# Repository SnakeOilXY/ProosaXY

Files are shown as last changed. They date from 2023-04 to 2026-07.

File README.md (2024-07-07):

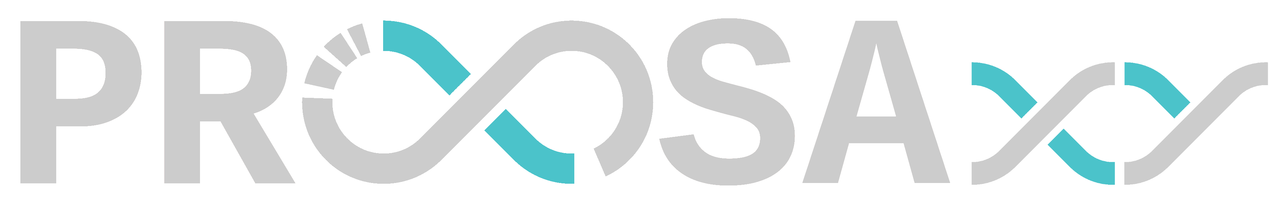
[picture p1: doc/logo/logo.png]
baner logo


<a href="https://discord.gg/WZVP2HuAag" style="height: 40px !important;">Join us on Discord</a>

<a href='https://www.amazon.jp/hz/wishlist/ls/2AHXTCG01RYAZ?ref_=wl_share' target='_blank'>Buy Me a spool at amazon Japan</a>

# ProosaXY
CoreXY conversion for Prusa MK3/S. This build is aiming at getting more performance out of your 6 years old machine with the lowest cost possible by re-using most the MK3/S stock parts.

## 1. Features

- Better performance (check input-shaper graph bellow).
- Semi-enclosure by default. Panels mount and top hat parts will be added later.
- ~~Dual z axis(default) or independent tripple Z axis(Optional)~~ Triple Z (independent or sync based on controller board) by default or dual Z(optional).
- Single v6 hotend(default) or mixed 2-in-1-out hotend(WIP).
- Optional AUX cooling fan.
- Semi-enclosured(default) or Fully-enclosured with top hat(comming soon).
- Our industrial leading SnakeOil technology :).

## 2. Status

- All the main parts design are completed. Test print result are posted in our [Discord server](https://discord.gg/WZVP2HuAag)
- All part STLs are exported. 
- Full BOM added 2023/07/11
- I'm working on a simple build log/manual. 
- For updates, please visit our [Discord server](https://discord.gg/WZVP2HuAag)

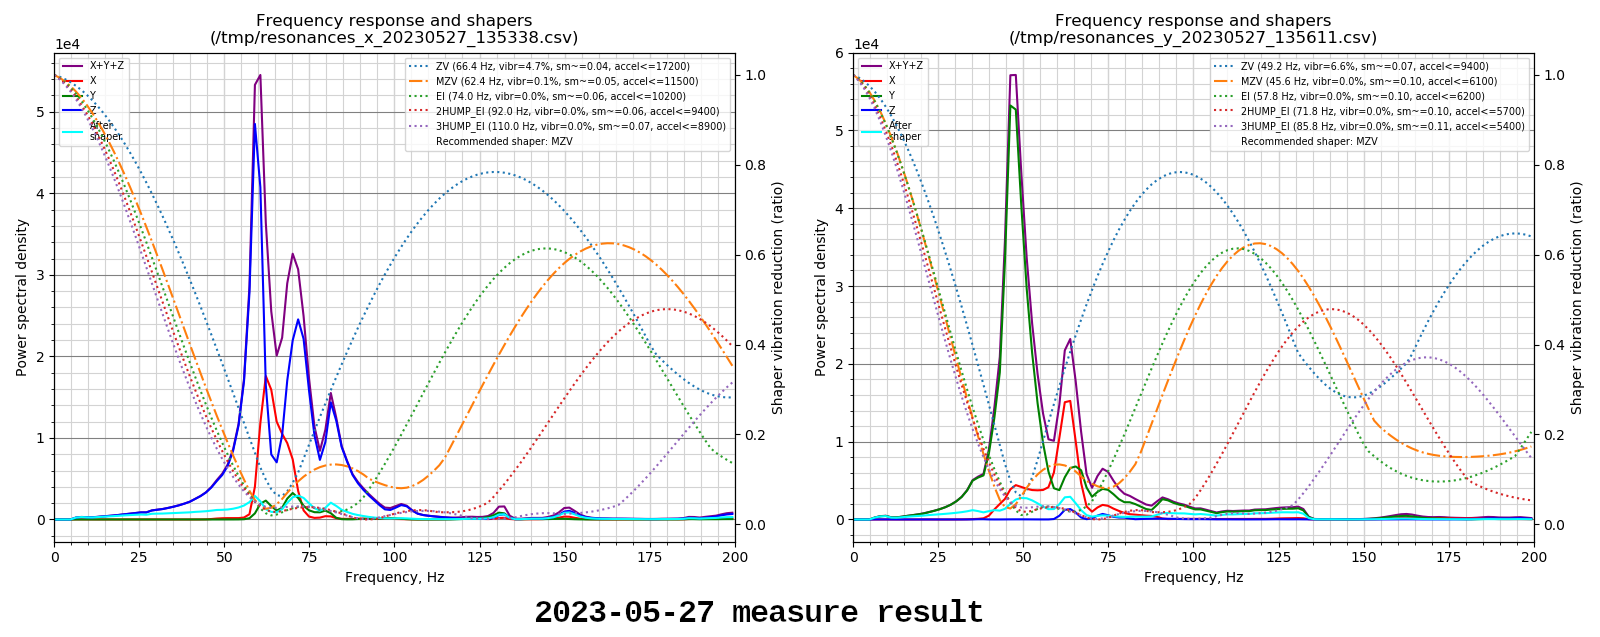
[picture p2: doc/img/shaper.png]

- The input-shaper calibration is quite good for an 8mm shaft machine, in my opinion. We have a recommended acceleration of about 6000 mm/s2 (which should be used as the limit for outer perimeter acceleration), and a higher maximum acceleration/speed, depending on how fast your motor can run.
- For some extra speed boost, check my [slicer plugin](https://github.com/SnakeOilXY/klipper-dynamic-scv-slicer-post-processing) (klipper firmware only)

## 3. Warning - read this

- This mod requires some drilling on the original frame, cutting the original motor leadscrew, and linear shafts. This drilling/cutting is easy enough to be done with a hand drill and a hacksaw **BUT THERE IS NO WAY BACK. You won't be able to convert back to the original MK3/s machine if you change your mind later.**
- Some small changes/patches might be needed after I have more test data and feedback..
- To keep the cost down and reuse old components, there are some trade-offs I made:
    - The machine is semi-enclosed by default and will need some printed panels and a top hats to fully enclose it.
    - To match the frame height, cutting the motor leadscrew and linear shafts is required.

## BOM

[Fabreeko ProosaXY Conversion Kit (Open Beta)](https://www.fabreeko.com/products/proosa-xy-conversion-for-mk3s-to-core-xy-by-snakeoilxy-open-beta) available now.

[>>> Bill of materials <<<](./doc/BOM/readme.md)

## 4. Test run videos and images

### 4.1 Prusa Mk4 12mins bonker benchy 

<table>
    <thead>
        <tr>
            <th></th>
            <th align="center">Mk4 bonker benchy</th>
            <th align="center">Real-world print</th>
        </tr>
    </thead>
    <tbody>
        <tr>
            <td>Video</td>
            <td align="center"><a href="https://youtu.be/1M5wx4Q0jNs" rel="nofollow">
            bonker benchy test print</a></td>
            <td align="center"><a href="https://youtu.be/Dink3JQ" rel="nofollow">
            normal test print</a></td>
        </tr>
        <tr>
            <td>Description</td>
            <td>I use the setting Prusa used on their mk4 12 mins benchy with accel pump up a little.</br>
            <a href="https://github.com/SnakeOilXY/ProosaXY/tree/master/doc/img/bonker-benchy">Print result (images)</a></br>
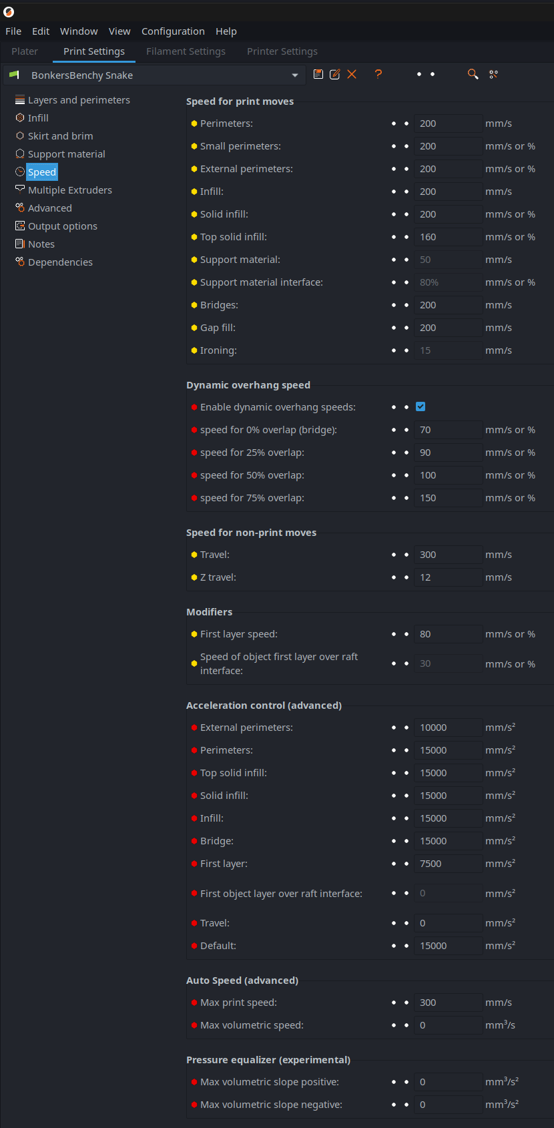
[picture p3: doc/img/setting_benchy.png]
            </td>
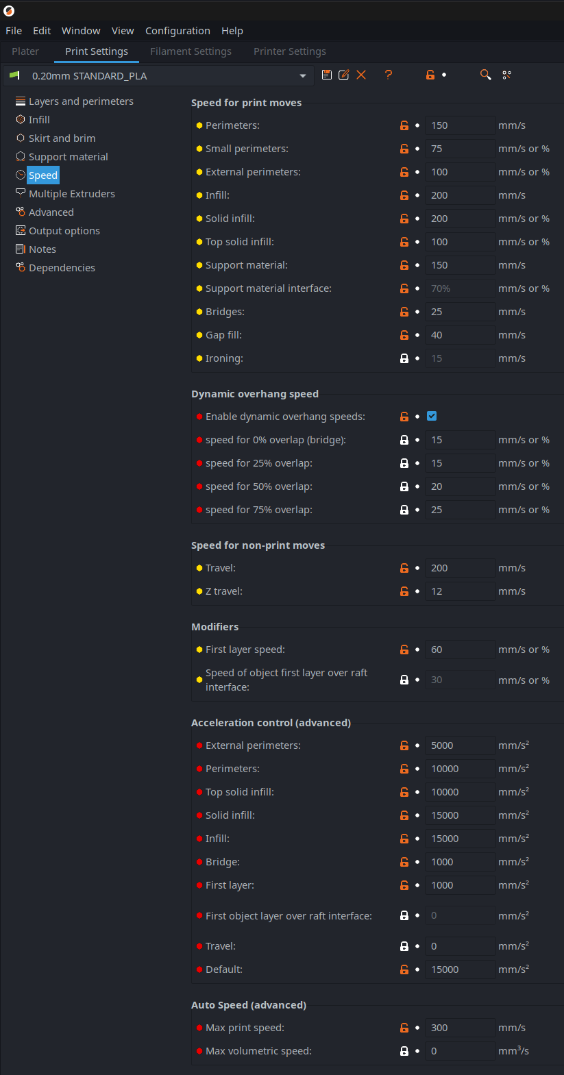
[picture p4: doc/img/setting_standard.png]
            <td></td>
        </tr>
    </tbody>
</table>

### 4.2 Images
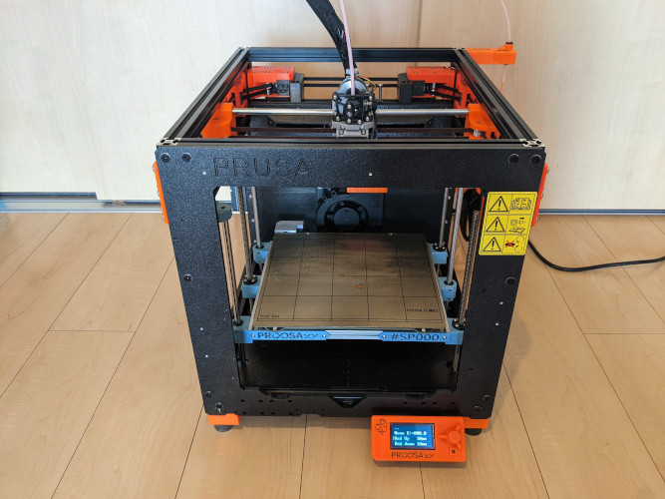
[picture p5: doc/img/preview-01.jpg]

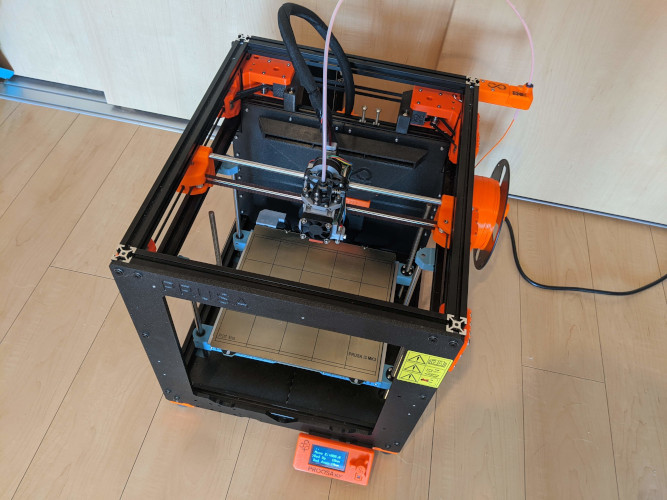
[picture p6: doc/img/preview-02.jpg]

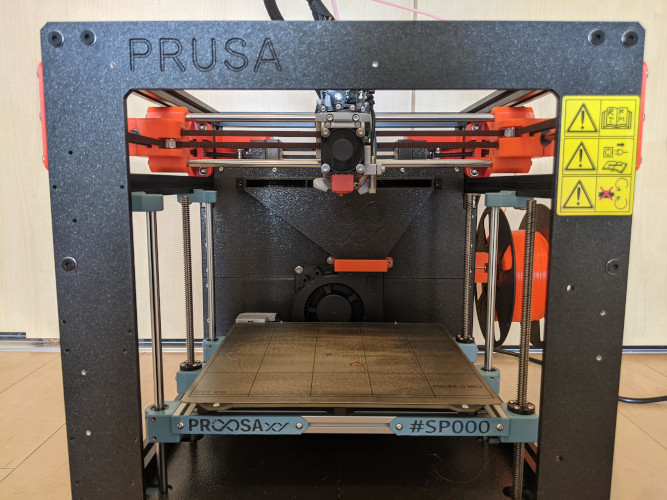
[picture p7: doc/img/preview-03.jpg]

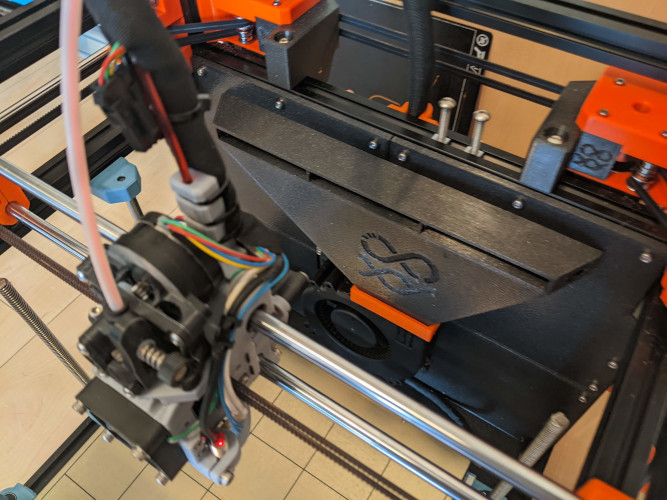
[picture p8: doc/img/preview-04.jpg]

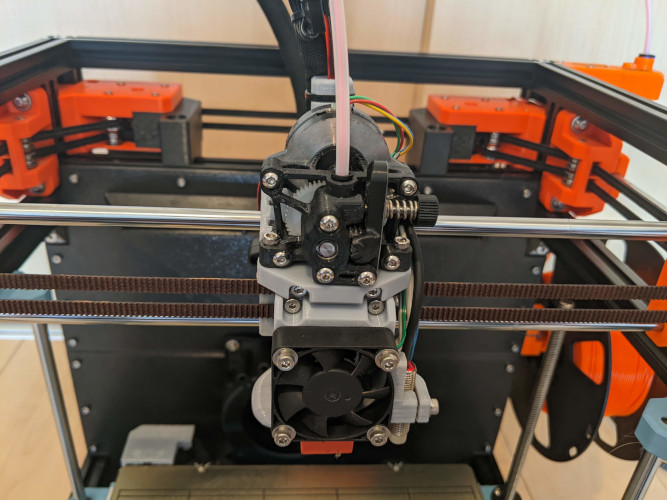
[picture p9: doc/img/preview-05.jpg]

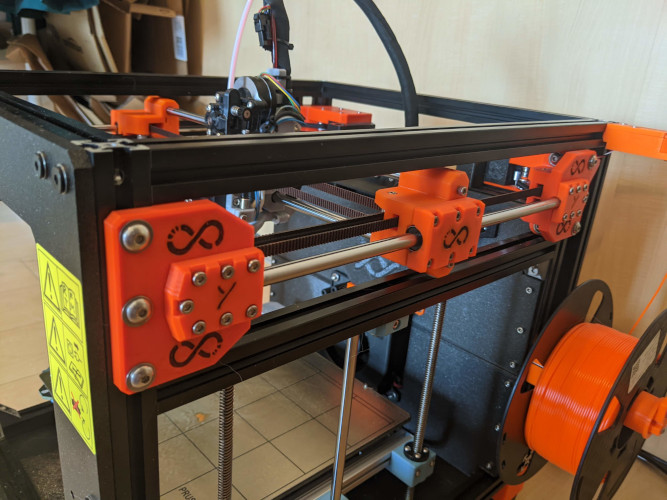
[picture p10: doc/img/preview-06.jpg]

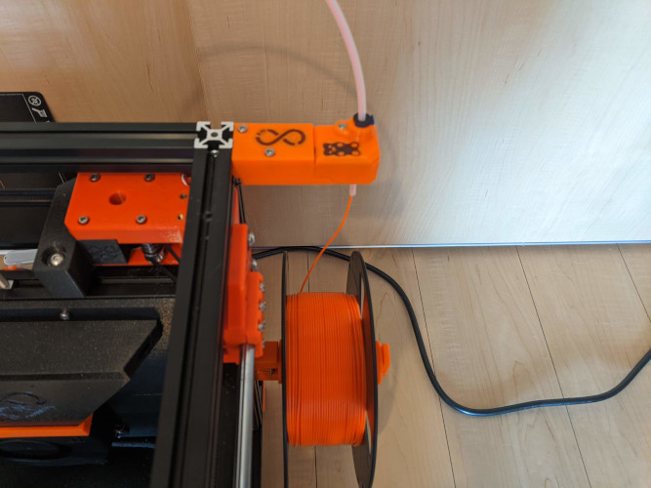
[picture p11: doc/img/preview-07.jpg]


## 5. Copyright Notice

This printer design use the following parts from other opensource project:
- Fan duct from [EVA 2.3](https://github.com/EVA-3D/eva-main)
- Filament sensor from [Bear Extruder And X Axis (BearExxa)](https://github.com/gregsaun/bear_extruder_and_x_axis)
- Sherpa mini extruder from [Annex Engineering](https://github.com/Annex-Engineering/Sherpa_Mini-Extruder)
- Din mounter from [Voron design](https://github.com/VoronDesign)
- Original hardwares from [Prusa MK3](https://github.com/prusa3d/Original-Prusa-i3)

### License

- [Sherpa mini extruder](https://github.com/Annex-Engineering/Sherpa_Mini-Extruder) is an original work of [Annex Engineering](https://github.com/Annex-Engineering), modified parts using their source code/design files are re-released under [ANNEX Engineering License](https://github.com/Annex-Engineering/ANNEX-Engineering-License-Agreement/blob/main/LICENSE.md).
- [EVA2](https://github.com/EVA-3D/eva-main) is an original work of [EVA-3D](https://github.com/EVA-3D), modified parts using their source code/design files are re-released under [GNU General Public License v3.0](https://github.com/EVA-3D/eva-main/blob/main/LICENSE)
- [Bear Extruder And X Axis (BearExxa)](https://github.com/gregsaun/bear_extruder_and_x_axis) is an original work of [Grégoire Saunier](https://github.com/gregsaun), modified parts using their source code/design files are re-released under [GNU General Public License v3.0](https://github.com/gregsaun/bear_extruder_and_x_axis/blob/master/LICENSE)
- [Voron]() is an original work of [Voron design](https://github.com/VoronDesign), modified parts using their source code/design files are re-released under [GNU General Public License v3.0](https://github.com/VoronDesign/Voron-2/blob/Voron2.4/LICENSE)
- [Prusa MK3](https://github.com/prusa3d/Original-Prusa-i3) is an original work of [Prusa3D](https://github.com/prusa3d), modified parts using their source code/design files are re-released under [GNU General Public License v2.0](https://github.com/prusa3d/Original-Prusa-i3/blob/MK3S/LICENSE)
- This printer design(ProosaXY), it's document and software are released under [GNU General Public License v3.0](https://github.com/SnakeOilXY/ProosaXY/blob/master/LICENSE)

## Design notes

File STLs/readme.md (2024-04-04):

# Print setting

## 1.Slicer config

- This is the setting I'm using but any other settings will work as long as the parts are strong enough.
- All STLs are oriented. (Please report if you find problem)
- Make sure your printer well calibrated.

<pre>Layer height : 0.2mm
Wall count : 5
Top/bottom layer : 5
Infill : 30% Gyroid 
Outer wall line width : 0.4mm
Inner wall line width : 0.45mm
Infill line width : 0.5mm
Most of the parts are designed to be printed without support(for exception, check the list bellow). You can enable "support on build plate only" for better overhang surface.
</pre>

### Parts require custom support

| | | |
|---|---|---|
| 3x_pom-nut-mounter.stl | | Need support on build plate |
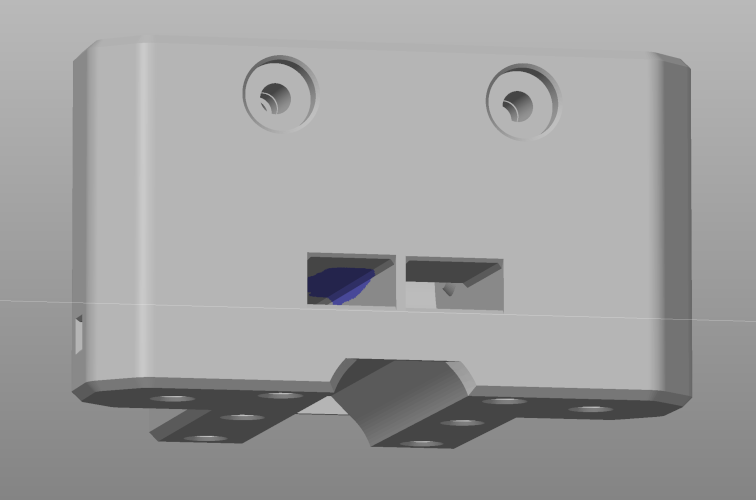
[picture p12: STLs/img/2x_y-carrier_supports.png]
2x_y-carrier_***
| 2x_y-carrier_***.stl |  | Custom support inside the channel due to some thin walls. |
| | | |

## 2.Filament

- PETG and higher temp-resistant filaments will work.
- Motor mount and tool head parts might require higher temp-resistant filament.
- Gillter or CF filled filaments might make the parts more brittle or creep.

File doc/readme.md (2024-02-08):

# Doc

- Extrusions drawing [pdf](./frame/frame-extrusion-drawing.pdf)
- Center frame drawing [pdf](./frame/mk3-center-frame-drilling.pdf)
- Bed frame drawing [pdf](./frame/mk3-bed-frame-drilling.pdf)

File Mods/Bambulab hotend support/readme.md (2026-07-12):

# ProosaXY Bambulab hotend support

The bambulab H2/P2 hotend/nozzles offers a good performance with a competitive price. And we have a bunch of aftermarket for this.

The main idea is to use the A1 heating assembly of aftermarket supplier like mellow or triangle lab.

Both offers Zirconia base plus Cooper block and 96W PTC heater (oem are 48W). Costs around 20-25€

The A1 heating assembly has better wires and known thermistor.

The idea of using H2/P2 nozzles are because they have longer melt distance than the A1 ones.

This idea was impossible to do before due the builtin tensioners, for that reason you need to fit the front belt tensioner mods and a proper X-carrier mod.

This aftermarket heating assembly it's intended to trick bambulab firmware/hardware restrictions that can only deliver 3.5A peak max on heater and later limit to 3A when printing, with this trick they boost the flow rate performance because the limitations made of the standard 48W heater.

We tested with 30mm3/s at 295ºC, the heater was at 50-60% duty cycle.

## IMPORTANT Printing instructions

The 1x_bambulab_fan_pinda_support requires to be printed with 0.15mm layer height, no supports required, they are modeled.

Enable supports for critical regions only on carrier_main_body parts and 0.15mm layer height.

## IMPORTANT bambulab version

Requires to print the bambulab style X-Carrier

Its intended to fit aftermarket or OEM heating assembly of Bambulab A1, may can work with H2 but not tested. The insulator part need to be printed with heat resistant material, ABS/ASA is not suitable for that piece. The heating assembly has two parts, the hot and the cold, the cold zone has no problem and it's where the mounting screws are fitted, but you need to protect the X-carrier from the heat, the hot zone go really hot.

PC+PBT+GF with HDT of 120ºC melts a bit on hot side, this material is perfect due if you don't anneal its anneal for itself when cooldown. and hold okay without problems.

PA12-CF it's also suitable, made the part of 1mm of thickness to don't have problems with creep. The final version will use a 1mm FR4 PCB, you can also use a universal prototiping board with that thickness and cut by hand. Or whatever you have that insulate with that thickness.

You can use also kapton tape also.

100 Hours of printing filaments at 275-290ºC.

The cold side screws are still thigtened.

<p style="text-align:center;">
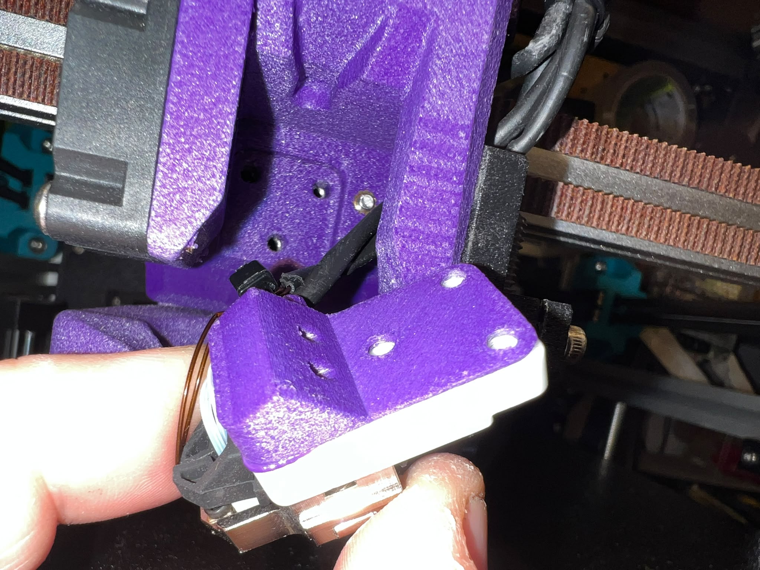
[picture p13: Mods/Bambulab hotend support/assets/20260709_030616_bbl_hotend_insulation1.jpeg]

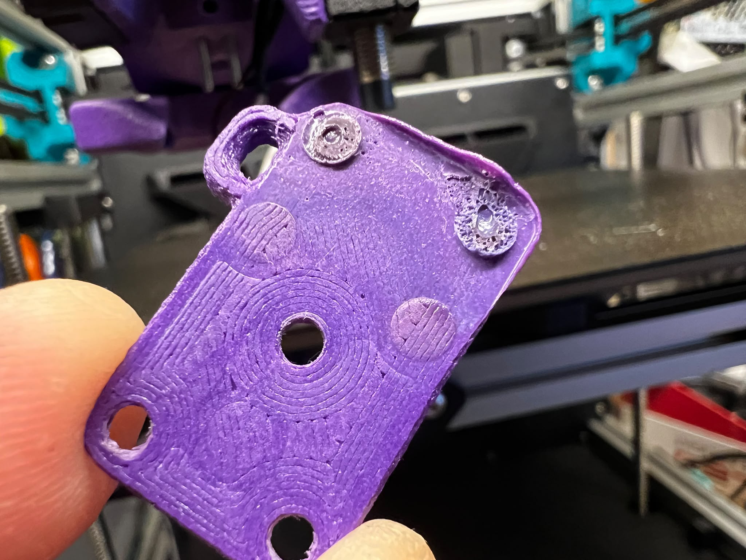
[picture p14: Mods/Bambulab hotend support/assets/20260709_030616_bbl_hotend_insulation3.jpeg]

</p>

The pc+pbt+gf do a great job insulating

<p style="text-align:center;">
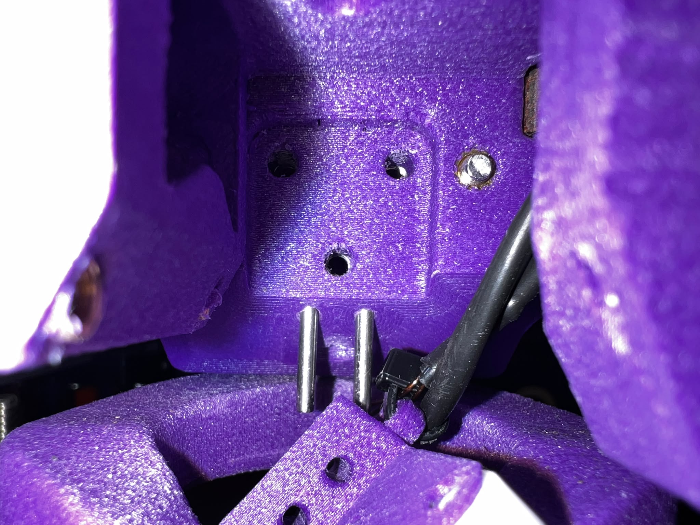
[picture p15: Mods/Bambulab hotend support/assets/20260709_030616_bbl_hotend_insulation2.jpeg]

</p>

You can also add kapton tape. The test was made without kapton tape.

<p style="text-align:center;">
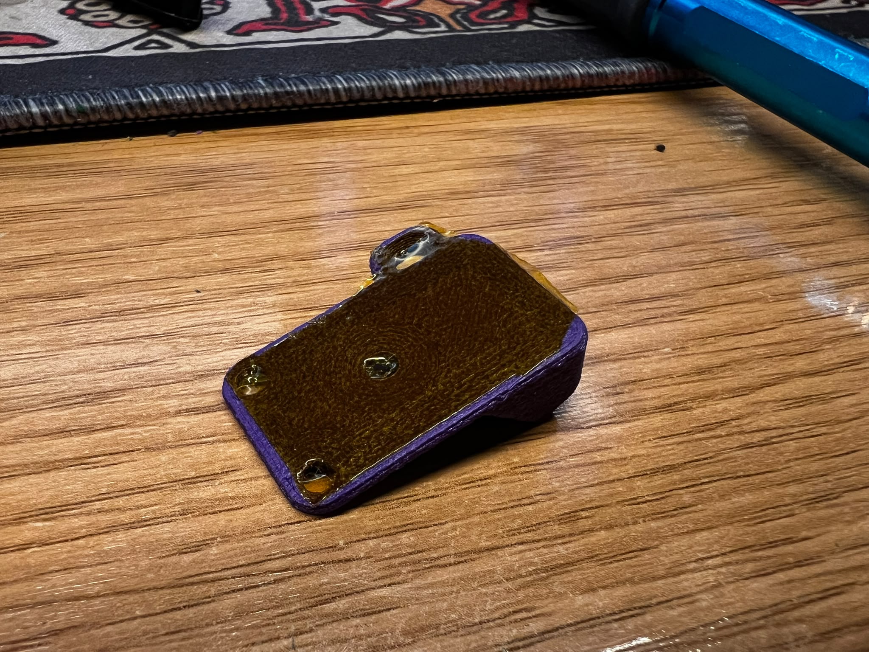
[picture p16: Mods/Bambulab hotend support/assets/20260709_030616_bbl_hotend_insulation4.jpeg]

</p>

Take in consideration that most of aftermarket developers advertise that even te cold side is hot

<p style="text-align:center;">
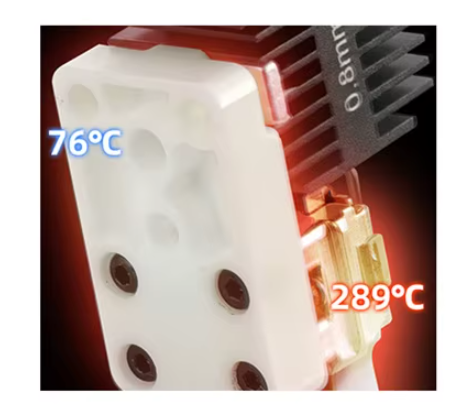
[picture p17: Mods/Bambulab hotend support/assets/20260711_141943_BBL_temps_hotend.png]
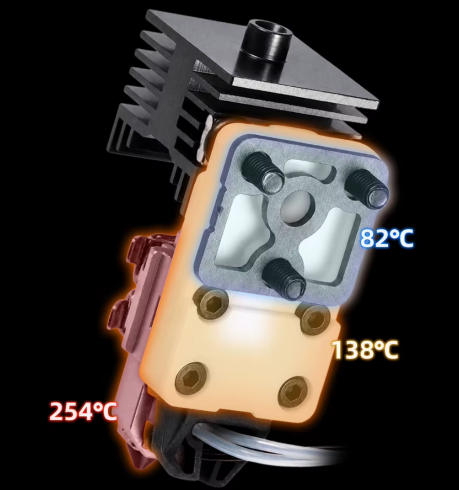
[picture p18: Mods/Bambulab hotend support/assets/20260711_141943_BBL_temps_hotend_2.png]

</p>

## Hotend insulator types

In this section we analyze some of the alternatives.

### Cheap alternative self printed PC+PBT+GF insulator

Unanealed version of this filament can work without problems, the cold side remains with the same thickness, the hot side melts a bit but when cold it self anneal.
Annealed version can work without problems.

### Easy and cheap alternative, PCB insulator

We added a gerber file to buy the pcb on your favorite website. Since it's very cheap we recommend this.

The PCB need to be 1mm thick. 5 pcbs on some website costs 4-5$ with shipping.

<p style="text-align:center;">
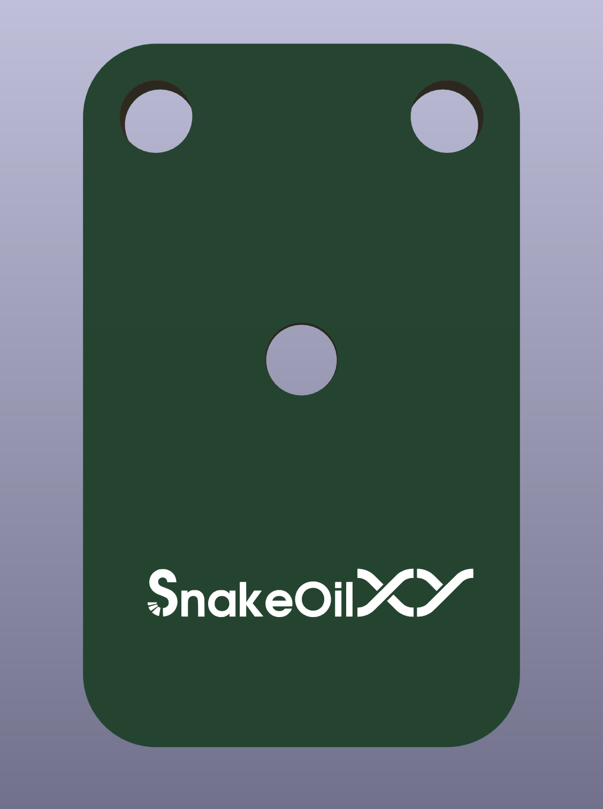
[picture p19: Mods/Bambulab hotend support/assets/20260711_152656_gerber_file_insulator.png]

</p>

### Another easy and cheap alternative.

Just upload the printed insulator and print with SLS/MJF nylon.

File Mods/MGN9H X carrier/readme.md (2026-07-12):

# ProosaXY MGN9H X-carrier toolhead

## Main advantage

With this carrier attached to linear guide instead of round LM8UU bearings you removed a lot of toolhead wiggle on hard accelerations that impact on printing quality at high accels/speeds.

Also have a more easy to fit belts in case of needed to do some maintenance.

It have a motor support to remove the wiggle produced by the weight of the stepper motor, this support it's only compatible with sherpa extruder.

## IMPORTANT printing instructions

You need to print with 0.15mm layer height all parts and enable supports. Due some organic structures and critical parts it's better to leave this to user. Because some filaments perform different than others on overhangs/z-distance of supports.

6-7 walls recomended.

## Compatibility with parts of LM8UU carrier

Except for bambulab version that is have an special carrier, all hotend mounts and extruder mounts of LM8UU are compatible with this, even the fan mounts.

Also the bambulab version can fit hotend mounts designed for LM8UU version, but you can fit the lower part, for example the V6 stabilizer, but we working on design these mounts to fit on bambulab version and maintain only one carrier.

## Reinforcements

Check the cad to see the reinforcements, the dowel pin ones they aren't 100% required but we recomend to install, also the M3 ones gives some support for M3x8 screws that fits the printed piece to the cart. Allowing to thigthen without material creep.

### Main body front

The M3 dowel pins are required to mount the belt clips

The M2x50 ones are not required but ensures a lot of rigidity

The body has slots within the printed piece to enforce more perimeters.

On bambulab version The M2x50 dowel pins are required to ensure rigidity and avoid material creep/loosening the screws.

<p style="text-align:center;">
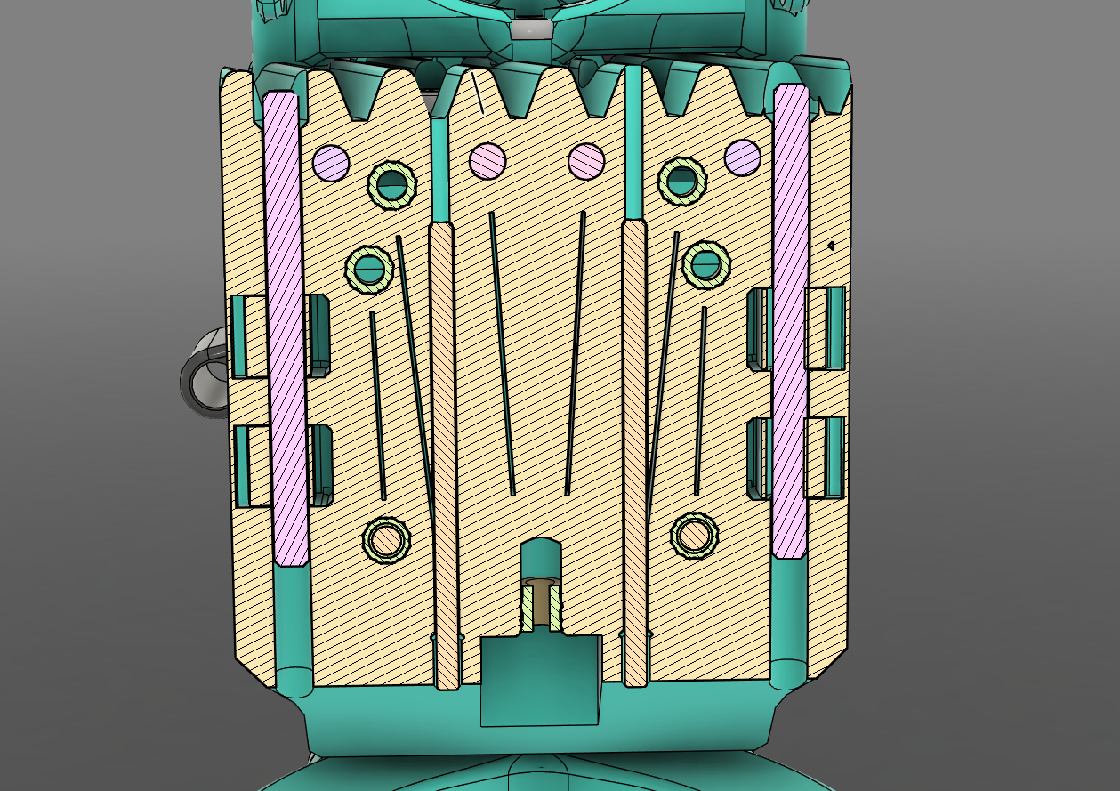
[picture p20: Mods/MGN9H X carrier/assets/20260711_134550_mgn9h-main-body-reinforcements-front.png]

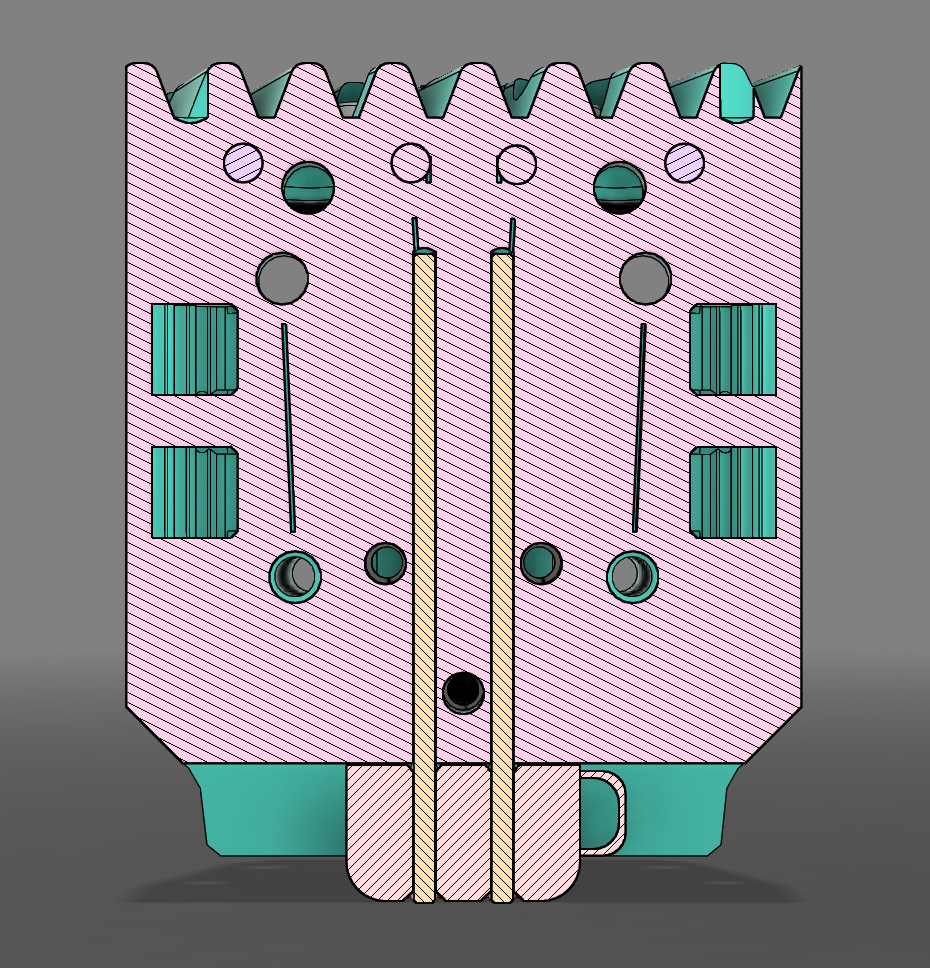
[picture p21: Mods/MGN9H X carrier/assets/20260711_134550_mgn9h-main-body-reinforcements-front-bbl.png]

</p>

### Main body top

These reinforcements are mandatory, you can run without but the carrier it's designed to have it.

<p style="text-align:center;">
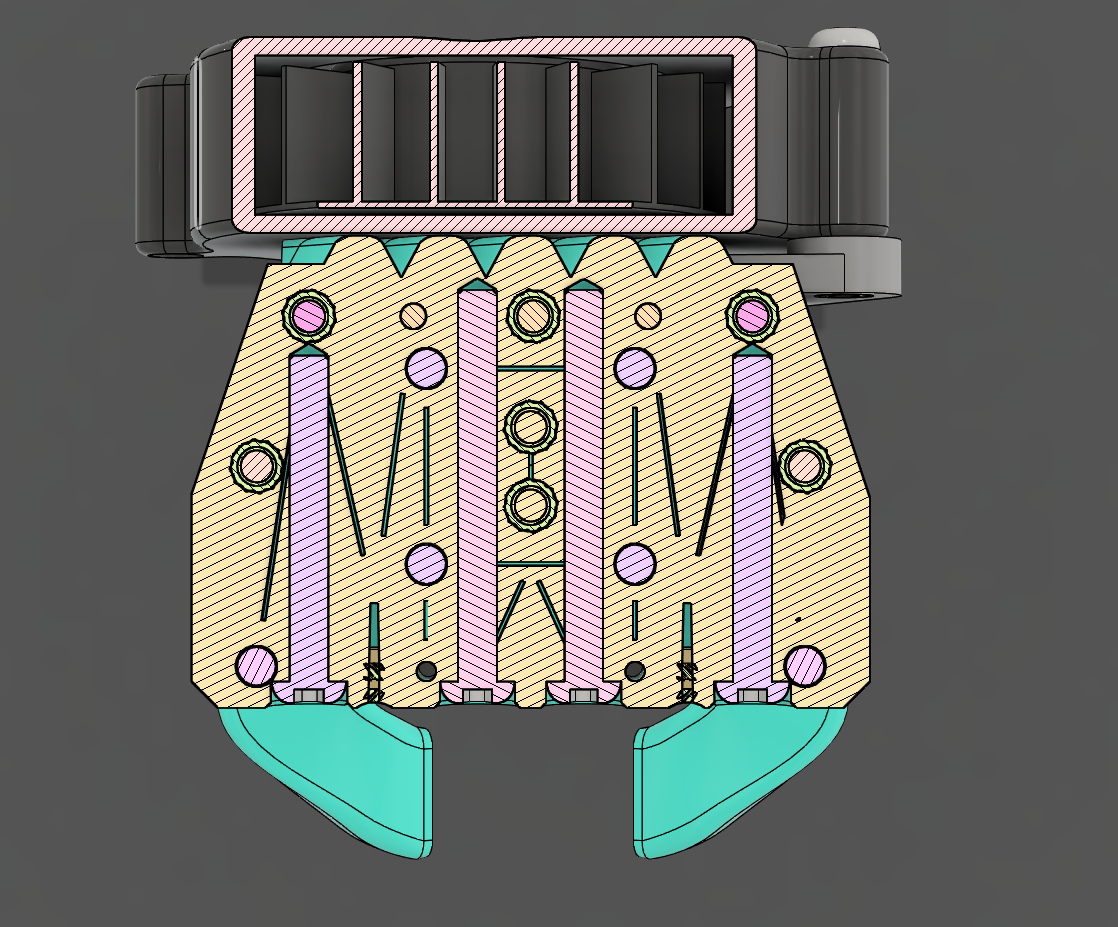
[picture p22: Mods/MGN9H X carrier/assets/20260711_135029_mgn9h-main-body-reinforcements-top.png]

</p>

### Rear part

These reinforcements are not critical, but it's recomended. The top M3x35 screw you can put as long you want, if you have a M3x60 you can fit. It reinforces the printed piece.

<p style="text-align:center;">
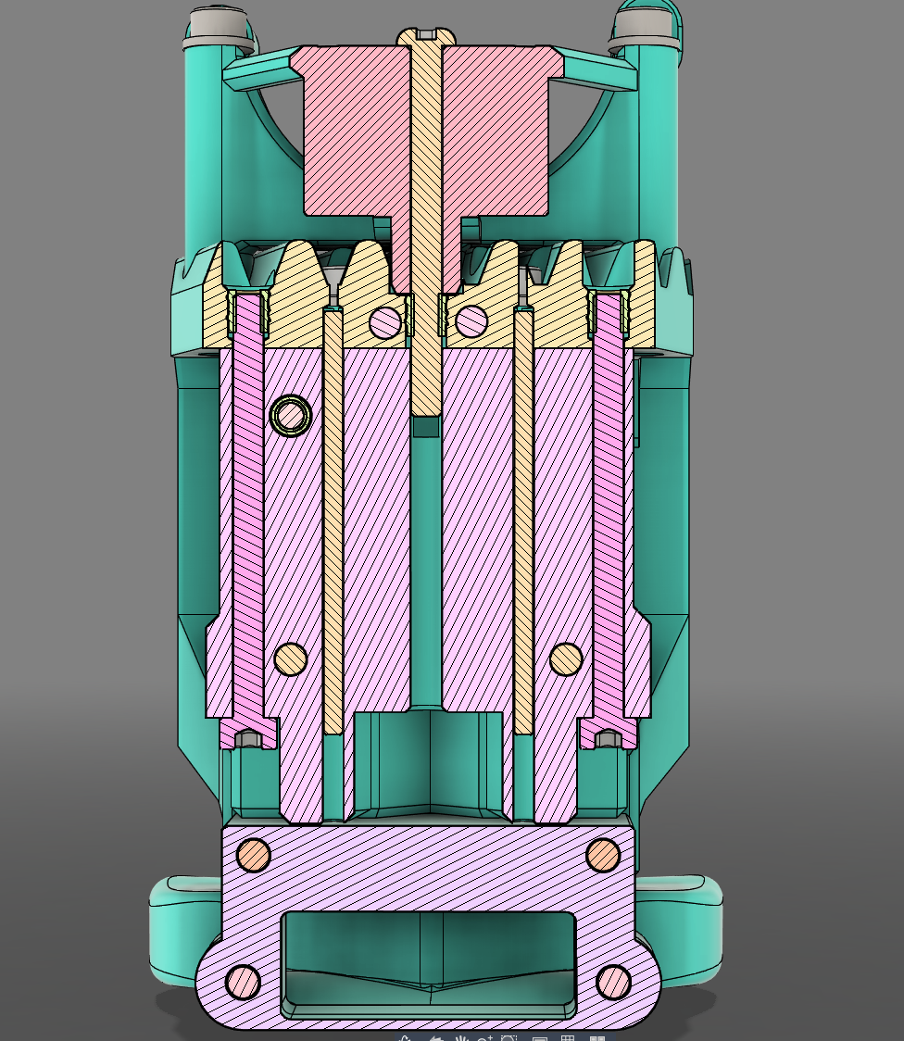
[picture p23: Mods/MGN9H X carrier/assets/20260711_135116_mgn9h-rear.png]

</p>

## BOM

| Part | Quanty | Notes |
| --- | --- | --- |
| M2x40 Dowel pin | 4 | for reinforcements |
| M3x40 Dowel pin | 2 | For Belt clip assembly |
| M3x4x4.2 Heat Insert | 14 | Standard ProosaXY heat insert |
| M3x10 BHCS | 2 | |
| M3x25 BHCS | 2 | for reinforcements |
| M3x30 BHCS | 2 | for reinforcements |
| M3x35 BHCS | 3 | |
| M3x8 SHCS | 4 | For MGN9H fixing |
| M3x10 SHCS | 2 | For motor support |
| M3x16 SHCS | 2 | For fan support |
| M3x20 SHCS | 2 | For motor support |
| M3x40 SHCS | 2 | For rear support |
| M3x3x7 Washer | 4 | |

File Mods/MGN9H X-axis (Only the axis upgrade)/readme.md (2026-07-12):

# ProosaXY MGN9H X axis

<p style="text-align:center;">
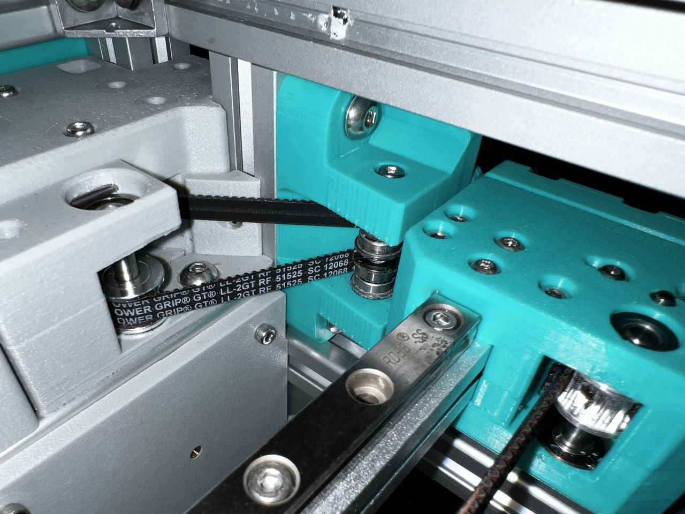
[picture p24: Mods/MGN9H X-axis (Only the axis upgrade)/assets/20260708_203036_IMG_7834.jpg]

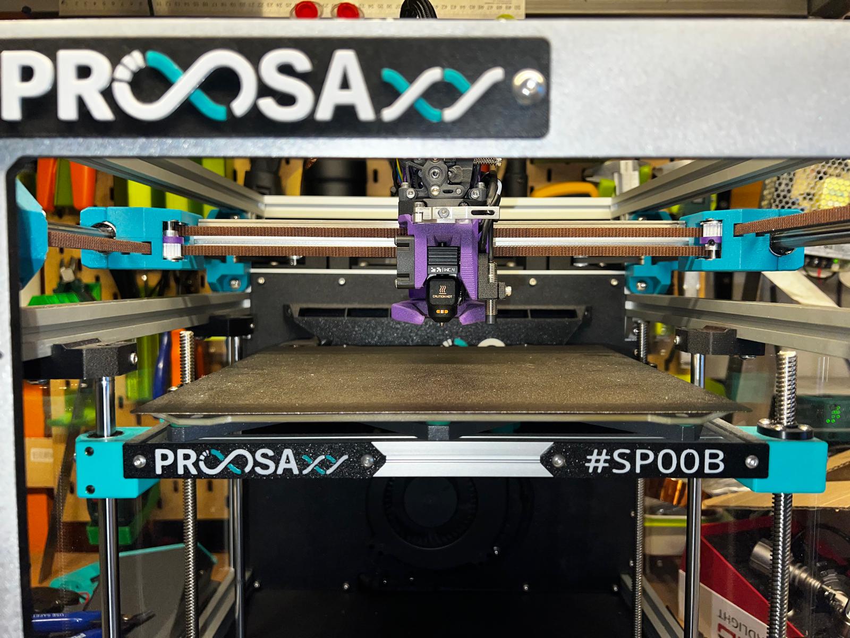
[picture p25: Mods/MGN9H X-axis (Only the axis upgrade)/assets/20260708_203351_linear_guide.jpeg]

</p>

This mod is intended to fit 1515 Alu Extrusion with MGN9 linear guide with H Cart.

Developed for ProosaHS but made the retrofit with LM8UU version, because the MGN9H toolhead improves A LOT the print quality when go with some accels and things speeds up a little. Because eliminates most of the toolhead wiggle.

## Upgrade Path

### ProosaXY maintaining LM8UU Y-axis

You need to install the following mods

* Front belt tensioners
* Short rear rod holders (included on this mod)
* Following BOM (we are reusing some screws from normal proosa)

| Part | Quanty | Notes |
| --- | --- | --- |
| 1515 Aluminum extrusion | 1 | 350mm for ProosaXY , 288mm for Proosa Mini, need to be misumi or Makerbeam XL |
| MGN9H | 1 | 305mm for ProosaXY , 244mm for Proosa Mini. |
| M3x8 SHCS | 8 | For the MGN9 linear guide assembly |
| M3x14 SHCS | 12 | Reused from ProosaXY |
| M3x30 SHCS | 10 | Can be BHCS |
| M3x12 BHCS | 8 | Can be SHCS |
| M3 Square nut | 18 | |
| M3x4x4.2 Heat Insert | 22 | Standard ProosaXY heat insert |
| M3x16 Dowel pin | 2 | |
| F623RS Flange Bearing | 4 | Reused from ProosaXY |
| M3x5x0.5 Washer | 2 | Reused from ProosaXY |
| 2x LM8UU Linear bearing | 4 | Reused from ProosaXY |

For narrow version (Halved 2mm), that allows to move the bed to the left 4mm and able to nozzle go outside the bed easy for purge bucket and others

| Part | Quanty | Notes |
| --- | --- | --- |
| M5x30 BHCS | 2 | |
| 20T 2GT Gates style idler | 2 | 10mm tall, 15mm OD , check CAD for details |
| M5x7x0.5 Washer | 4 | |

For standard version.

| Part | Quanty | Notes |
| --- | --- | --- |
| M5x30 BHCS | 2 | |
| 20T 2GT 8.5mm height toothed idler | 2 | You may will reuse this if you already have the 20T mod |

For Live idler version

| Part | Quanty | Notes |
| --- | --- | --- |
| M5x30 Dowel pin | 2 | |
| F695 Flanged bearing  | 4 | |
| M5x7x0.5 Washer | 4 | |
| M3x5x7 Washer | 4 | |
| M3x4x4.2 Heat Insert  | 8 | |
| M3x6 BHSC | 4 | |
| M3x8 grub | 4 | You can use also a normal screw but will protude and makes the printer ugly |
| 20T AF Pulley / dehub | 2 | You can use dehubbed 20T pulley, you need to sand a bit the screws to make shorter, to not rub with the other belt,  also you can use AF style pulley if it comes with M2.5/M2 grub screw, the ones with M3 screw may damage the belt on time. You can also use press fit pulley. |

### ProosaXY Upgrading to 10mm rods on Y axis or Proosa Mini

The same of live idler LM8UU upgrade path but printing the 10mm parts.

Check your bearing type, if you are upgrading from Proosa Mini that comes with LM10LUU you need to print the LM10LUU parts, if not we recomend to buy LM10UU bearings.

You will need 4.

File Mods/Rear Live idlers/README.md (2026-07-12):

# ProosaXY Rear live idlers

## 1. Intro

This upgrade is made originally for the ProosaXY HS but can be retrofitted to Stock ProosaXY if you want to fit live idlers instead of normal idlers.

The main advantage of live idlers it's we can fit big bearings on toothed idlers. Making it suitable for high speed / accelerations.

This mod is intended to fit without reprint the motor mounts.

<p style="text-align:center;">
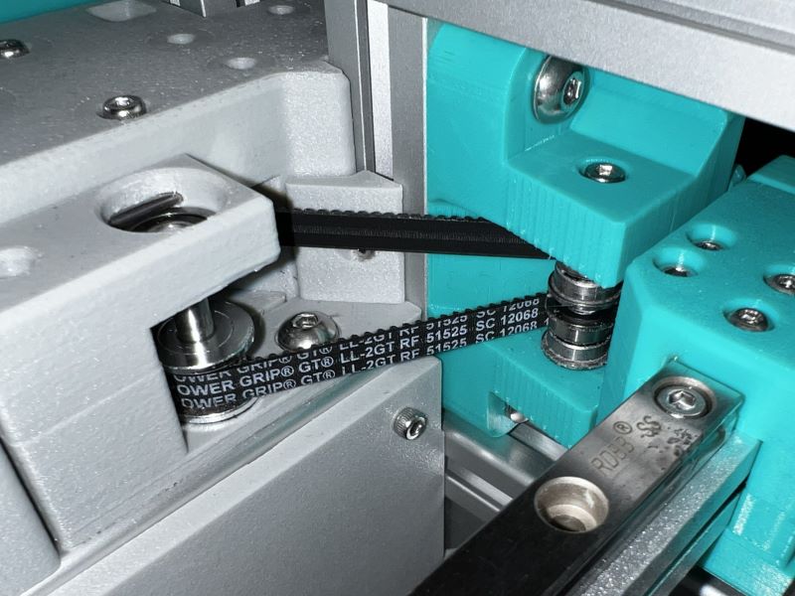
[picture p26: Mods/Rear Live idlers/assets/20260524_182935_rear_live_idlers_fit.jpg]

</p>

This live idler uses 2x30mm dowel pins to lock in place the top F695RS bearing and reinforce the printed part. the idler is mounted right in front of motor mounts, on the same extrusions.

<p style="text-align:center;">
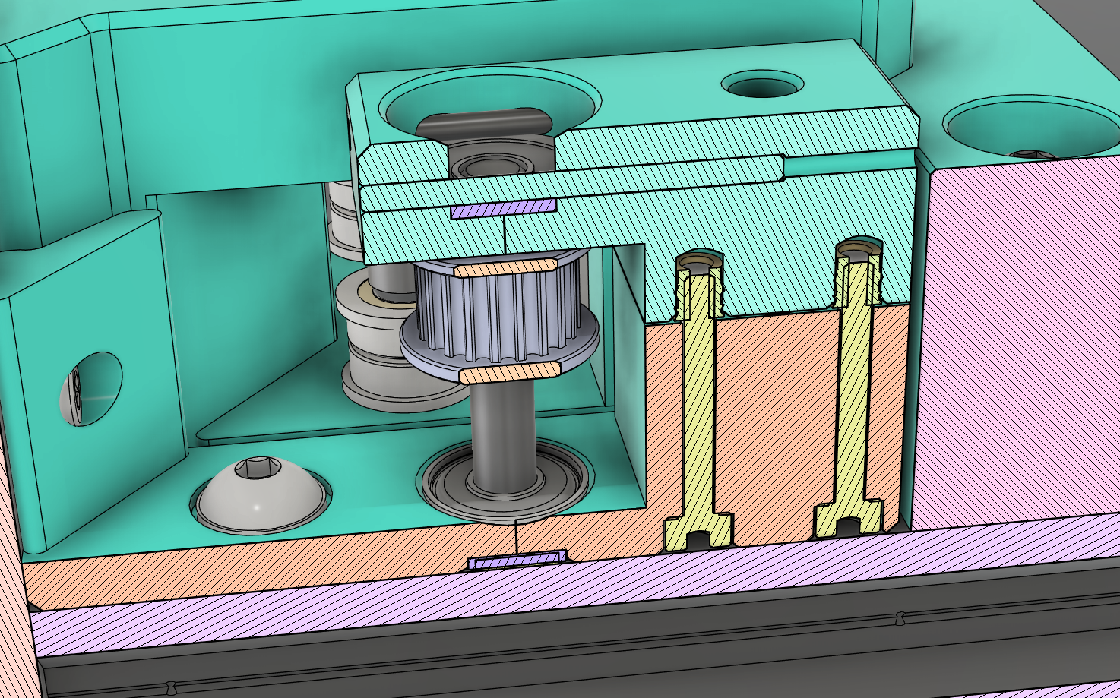
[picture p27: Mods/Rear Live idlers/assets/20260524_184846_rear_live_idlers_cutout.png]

</p>

## 2. Printing instructions

Due the stress that this part need to support it's recommended to print with carbon filled filament but not mandatory, and at least 7 walls and 7 top/bottom surfaces.

All parts comes with printable supports, no need to add your custom supports.

## 3. BOM (for two rear idlers)

| Name | Units | Notes |
| --- | ----- | --- |
| M3x20 SHSC | 8 | You can fit BHSC instead, but the pocket is made for SHSC |
| M3x8 SHSC | 2 | |
| M5x10 BHSC | 2 | |
| M5x16 BHCS | 2 | |
| M5x7x1 Washer | 4 | |
| M3 2020 T-nut | 2 | |
| M5 2020 T-nut | 4 | |
| M3x4x4.2 Heat Insert | 8 | Stock ProosaXY heat inserts |
| M2x30 dowel Pin | 4 | Can be longer if you have |
| M3x30 dowel pin | 2 | Can be longer if you have |
| 20T 2GT pulley | 2 | Check the next section for details |
| F695RS Bearings | 4 | Flanged bearings |

## 4. 20T 2GT Pulley

TLDR: You can use whatever you want if have 5MM ID

Because we have room we let the posibility of you can fit whatever you want, even a 16T Pulley, this is not tested, if you test ping us on discord :).

Our recomendation is to use AF Type Pulleys, to save money, you dont need to dehub good 20T pulleys, you can fit as is without dehub.

Along it meet the 2GT belt cut it's good to go.

<p style="text-align:center;">
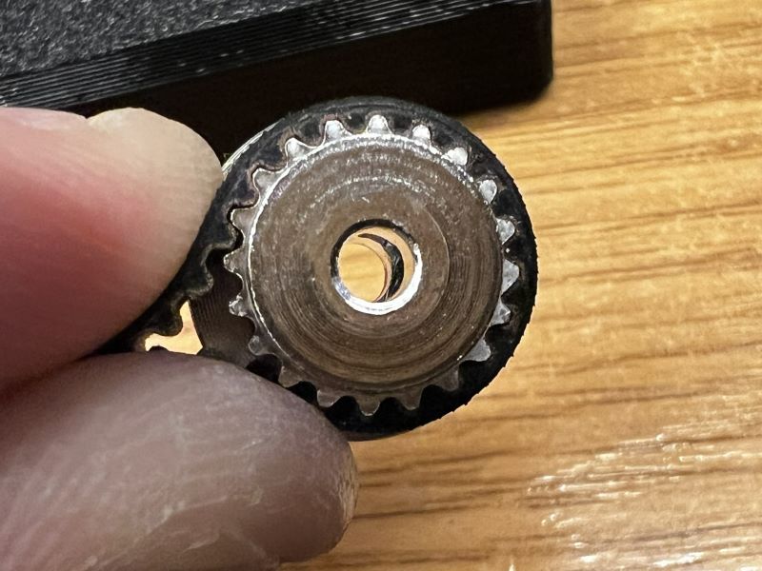
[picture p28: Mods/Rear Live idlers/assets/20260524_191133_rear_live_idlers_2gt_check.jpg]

</p>

If you plan to fit the MGN9H X axis mod we encourage to buy AF type pulleys, because on the carriers you can't fit no-dehub pulleys

## 5. Assembly

The design takes in consideration that it's very difficult to have perfect sized small holes, and it's very difficult to have a "universal" clearance for 2mm holes that needs to be perfect to 2mm.

You need to bore up the holes for the 2mm dowel pins ensure smooth operation. If not you will have some difficulties to remove the dowel pins if needed.

The M3x8 screw is only ensure the printed part is centered and put in their correct position, no need to thighten fully, the only screws that need to be thigten fully are the M5 ones, if you notice the idler doesn't run smooth you need to loose a bit the M3x8 extrusion screw.

The F695RS is press fit on both sides. On top is fixed in place using the two dowel pins, on the bottom place is fixed in place when mounted on the extrusion.

<p style="text-align:center;">
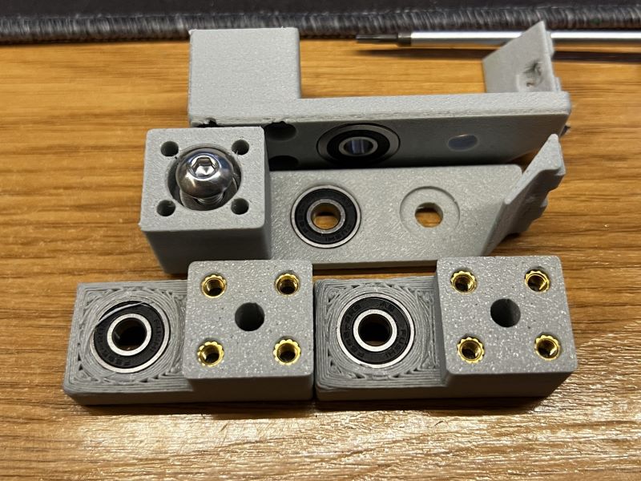
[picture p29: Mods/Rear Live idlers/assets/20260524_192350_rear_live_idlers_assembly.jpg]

</p>

Assemble both parts (bottom and top) with the M5x16 + M5 washer inside. The left pulley is on top, the right pulley on bottom place, you can fix in place if you want, if your pulley has screws thigten and put threadlocker if your pulley is pressfit you can use loctite 648 to fix in place.

<p style="text-align:center;">
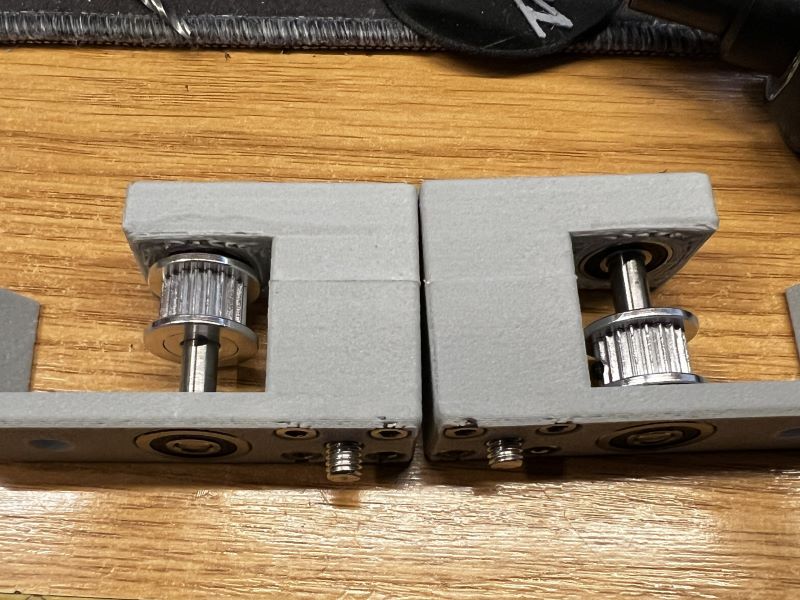
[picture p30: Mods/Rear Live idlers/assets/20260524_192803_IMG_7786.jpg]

</p>

Do not forget to remove the 16T idlers of motor mounts and replace it with the printed spacers. You need to print this specific spacers, need to be thin to allow the belt pass without grinding.

<p style="text-align:center;">
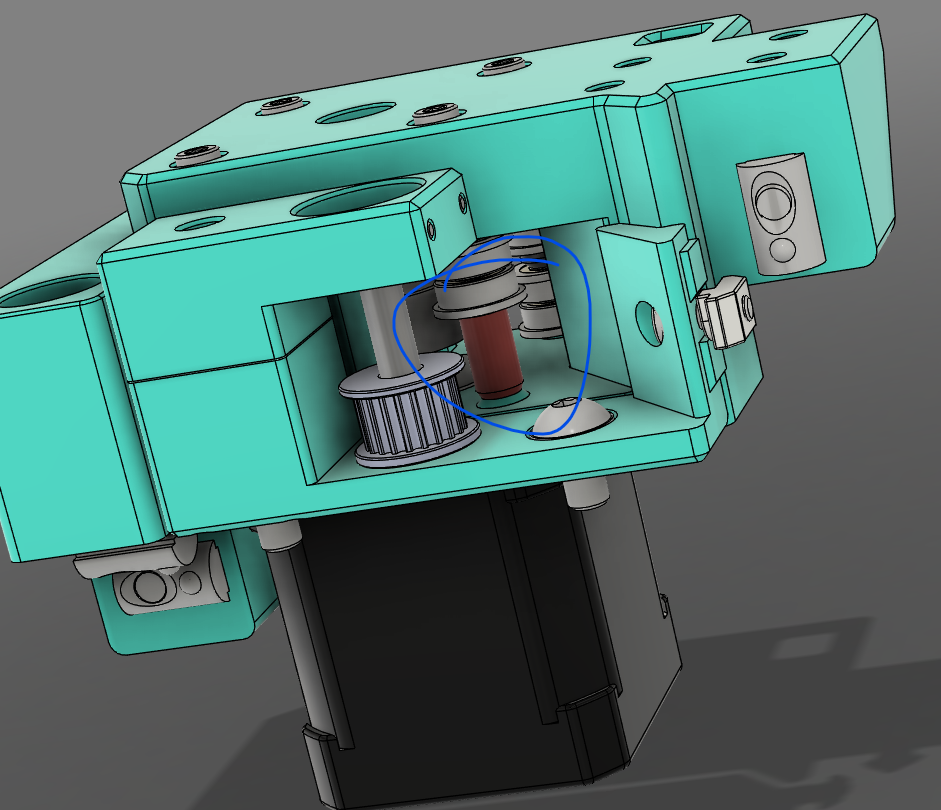
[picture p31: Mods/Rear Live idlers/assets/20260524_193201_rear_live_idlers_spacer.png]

</p>

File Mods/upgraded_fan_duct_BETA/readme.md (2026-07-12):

# Upgraded fan duct

This is a upgraded version of the fan duct.

The standard one of the Proosa it's a bit weak, work with standard 5015 fan of prusa but doesn't perfom very well on high pressure/flow 5015.

There is the comparison between the Standard proosa duct and alpha version of the new duct (variation of tri-horn of eva)

All test were made with the same brand of PLA, 230ºC and Proosa Mini / Proosa HS std profile with min layer time removed (1s) and no z-hop, The fan it's the same, GSD Time 8500RPM at 100%

We have a improvement but not much.

<p style="text-align:center;">
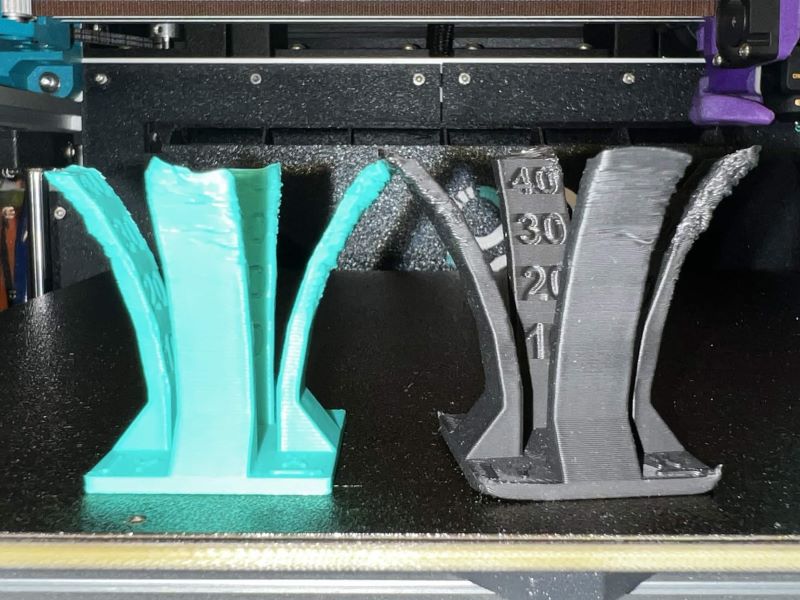
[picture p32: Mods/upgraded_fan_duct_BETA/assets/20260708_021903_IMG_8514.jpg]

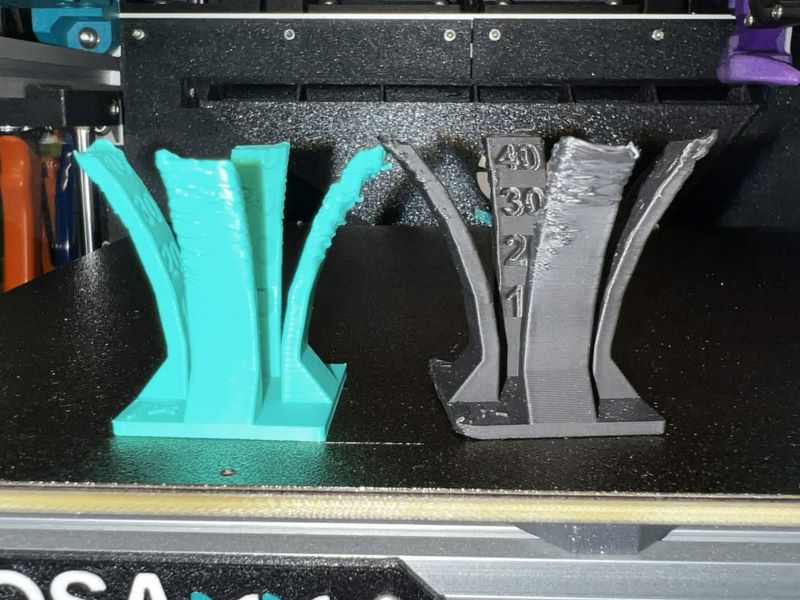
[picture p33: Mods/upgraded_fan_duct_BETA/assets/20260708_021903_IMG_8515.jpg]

</p>

With the new beta fan duct the improvement is massive. Almost finished the test, with more layer time will finished the test, but the nozzle deatached the printed part from the bed because hits curled edges.

<p style="text-align:center;">
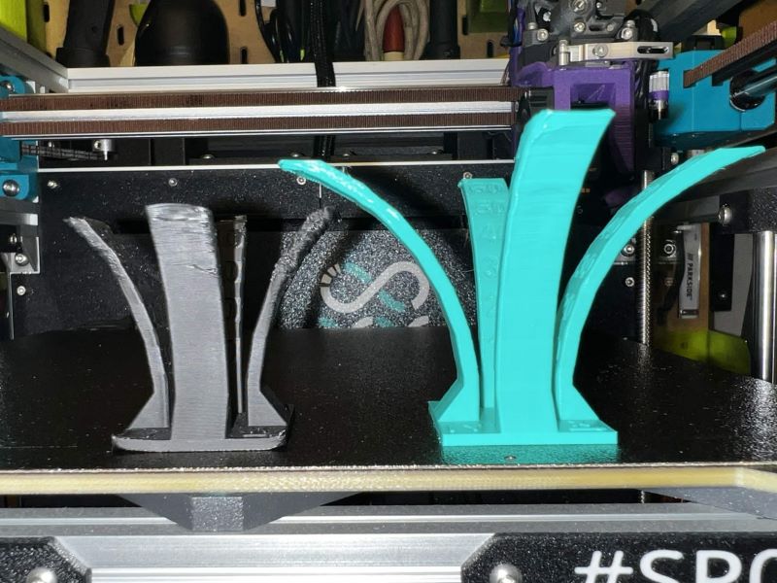
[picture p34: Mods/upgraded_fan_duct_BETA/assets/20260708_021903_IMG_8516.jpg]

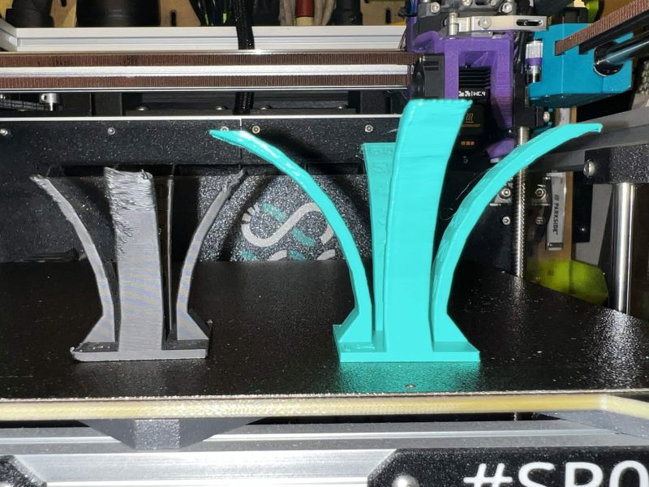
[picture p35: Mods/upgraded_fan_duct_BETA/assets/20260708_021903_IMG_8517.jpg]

</p>
<p style="text-align:center;">

</p>

Video showing the nozzle hitting the printed part.

<p style="text-align:center;">

</p>

Even the bridging improved a lot (video bridging)

<p style="text-align:center;">

</p>

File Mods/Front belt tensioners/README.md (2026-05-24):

# ProosaXY Front belt tensioners

## 1. Intro

This upgrade is made originally for the ProosaXY HS but can be retrofitted to Stock ProosaXY with 8mm rods if you prefer to use front belt tensioners or maybe you want to fit a custom toolhead

Due it's made originally for the ProosaXY HS that uses 10mm bearings it's 5mm shorter, if you fit with stock 8mm y-carrier you will gain extra 5mm travel on Y, take in consideration an modify your config an add and extra -5mm to Y or use it :)

<p style="text-align:center;">

</p>

This compact belt tensioner uses 2mm dowel pins as a guide and features double screws for tension adjustment, in fact you can use only one due the 2mm guides but it's recommended to tighten both to ensure the best reliability. It's capable of 15mm of travel, to use the last 5mm of travel you need to change the screws for others 5mm shorter, because we are using the extrusion pocket to permit the screw protude.

<p style="text-align:center;">

</p>

## 1.2. Demo

This is a video of a demo of the belt tensioner and the travel.

<p style="text-align:center;">

</p>

## 2. Printing instructions

Use the stock SNAKOIL settings for all parts except the bearing holder, for bearing hoder print solid if you can or at least 7 perimeters with 7 top/bottom layers.

## 3. BOM (for two front belt tensioners)

Here only appears the extra hardware needed, not the full bom.

| Name | Units | Notes |
| --- | ----- | --- |
| M3x10 SHSC | 2 | Replaced one M3x14 SHSC from the y-rod-cap |
| M3x25 SHSC | 4 | For belt tensioner itself |
| M3x20 BHSC | 2 | Can be longer but it will protude and will look ugly |
| M3x25 BHSC | 2 | Can be longer but it will protude and will look ugly |
| M3x30 BHSC | 4 | Can be longer but it will protude and will look ugly |
| M3x4x4.2 Heat Insert | 12 | Stock ProosaXY heat inserts |
| M3x5x0.5 Washer | 4 | |
| M2x30 dowel Pin | 8 | For Belt tensioner guide |
| M3x16 dowel pin | 2 | For bearing stack axle |

## 4. Assembly

The design takes in consideration that it's very difficult to have perfect sized small holes, and it's very difficult to have a "universal" clearance for 2 and 3mm holes that needs to be perfect to 3mm or 2mm.

You need to bore up the holes for the 2mm dowel pins and the two 3mm holes for passtru belt tensioner to ensure smooth operation. The dowel pins need to move smooth on belt tensioner.

Then assemble the bearing stack with the 3x16mm dowel pin and click in place.

<p style="text-align:center;">

</p>

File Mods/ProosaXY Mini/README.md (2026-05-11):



# ProosaXY MINI

This is the MINI version of ProosaXY using a Prusa MINI as a donor. Transforming your old printer on a beast with multicolour print capable if you want reusing most of the stock parts.

## 1. Features

- Better performance printing at 150/300mm/s 15/20K and 600mm/s-40k for travels.
- Semi-enclosure by default. Panels mount and top hat parts will be added later.
- Dual Z axis with independent drivers. (No more skew) with Z-tilt
- 180x180x210 build volume (You can use even 200x200x210 if the base of the print fits within 180x180 print surface.
- MMU capable (tradrack support)
- Semi-enclosured(default) or Fully-enclosured with top hat(comming soon).
- Our industrial leading SnakeOil technology :).

## 2. Warning - read this

- This mod requires cutting the original motor leadscrew, and linear shafts. This utting is easy enough to be done with hacksaw or other tools**BUT THERE IS NO WAY BACK. You won't be able to convert back to the original MINI machine if you change your mind later.**

## 3. Test run videos and images

### 3.1 Images

<p style="text-align:center;">
 
</p>

### 3.2 Videos

Printing random things

<p style="text-align:center;">
 
</p>

Printing clearance test.

<p style="text-align:center;">
 
</p>

Printing tall object (full height)

<p style="text-align:center;">
 
</p>

### 3.3 Printing settings

The printing settings of the videos are the following. Intended for fast-quality prints.

*Note: This settings are with OMC HE19 Steppers running at 1amp.*

**Speeds**

* 150mm/s External walls
* 250mm/s internal walls
* 300mm/s solid infill
* 350mm/s low dense infill
* 80mm/s top infill
* 600mm/s travel

**Accels**

* 15K default
* 10K external walls
* 20K internal walls
* 25K infill
* 5K top infill
* 40K travels

**Jerk/SCV**

* 15mm/s default
* 15mm/s external walls
* 20mm/s internal walls
* 30mm/s infill
* 10mm/s solid infill
* 40mm/s travel

Only Z-hop on top surfaces

### 3.4 Build your own Proosa XY :)

Check README on doc folder.
The bom is located here: [ BOM (GOOGLE DOCS), check Proosa Mini tab](https://docs.google.com/spreadsheets/d/1j1bnA8rNjDqpTVEdiqrsRlNeggI6PYRAoSBm1F8bvCs/edit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)

Check the CAD file under src/step section :)

</a>

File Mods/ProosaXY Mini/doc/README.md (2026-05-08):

# ProosaXY Mini build

## 1. FAQ

* Love this build but.... I need a Mini to make this build?

No, indeed, on some circunstances it's better to self source instead of buying a Mini to do this mod. If you have already a Mini or you find a cheap Mini you can use as a donor :)

The only part that is a bit difficult to source is the heated bed, you can buy a brand new one on Aliexpress.

* Where is the complete assembly guide of this printer?

Like the ProosaXY no guide available, only the step file of the standard ProosaXY and the discord, we put some help on this repo, but you are welcome to our discord :)

* There is no kit available like the ProosaXY ?

At this moment no. You will need to source all by yourself, we recommended to buy the extrusions already cutted and you only make the drills and taps.

* Where is the Step file of the ProosaXY Mini?

At this moment to avoid to delay the release to much we don't have at the moment, our team it's very small. But you can use instead the step file of the standard ProosaXY, this printer is essentially a small version of ProosaXY with minor differences.

## 2. BOM

The bom is located here: [ BOM (GOOGLE DOCS), check Proosa Mini tab](https://docs.google.com/spreadsheets/d/1j1bnA8rNjDqpTVEdiqrsRlNeggI6PYRAoSBm1F8bvCs/edit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)

### 2.1 Optional upgrades / options

#### 2.1.1 TR8x4 vs TR8x8 lead screw

The Mini uses TR8x4 lead screw to avoid to push to much the Z stepper holding the X-axis, you need to pair with another TR8x4, on our experience Prusa often uses a slighty different pitch on some of their Z steppers, you can pair without problems with other Z stepper of Mini but a standard TR8X4 lead screw is not tested, the #SP00F proosa it's built using two brand new TR8x8 steppers.

#### 2.1.2 Fresh LM8UU bearings

Why need to buy 3 LM8UU bearings if only need 2 ? Unless your mini comes with Misumi bearings... if your mini comes with noname bearings, put fresh new bearings. Trust me.

Stuck row of balls with missing ones.

<p style="text-align:center;">

</p>

Smooth rods destroyed, you can also reuse if you rotate to avoid the scores on the rod.

<p style="text-align:center;">


</p>

#### 2.1.3 Better X/Y motors

Stock steppers of Mini comes from the old reliable MK3S, very high inductance, very good to run with very low current with good torque on very low speeds and accels, very bad for high speed applications.

If you want to go further with stock steppers you need to know the current limit its about 0.6-0.65 amps and some printing accels/speeds [based on my old Klippericed MK3s bedslinger](https://www.youtube.com/watch?v=eHqDQD0xJSYhttps:/)

* External walls 3K / 140mm/s / 5mm/s SCV
* Internal walls 5K / 140mm/s / 7mm/s SCV
* Low density infill 8K / 200mm/s / 9mm/s SCV
* Solid infill 8K / 200mm/s / 9mm/s SCV
* Top surfaces 3K / 80mm/s / 9mm/s SCV
* travel 8K / 350mm/s / 12mm/s SCV
* Stepper motors horny like hell (expect 80-85ºC)

Yeah it's not that bad when you comes from 1-2K accels and poor speeds but...it's a 20€ upgrade that makes huge difference.

Otherwise, the stock steppers can't go double sheared, expect internal bearing failure over time with these heat + speeds + accels.

<p style="text-align:center;">

</p>

#### 2.1.4 8mm linear shaft

You need H6 or better tolerance shafts. AKA, the rod needs to measure at minimum 7.991mm , if the rod measure below these dimension the bearing will not fit very well and you will have problems of internal play. Some aliexpress vendors sell 7.970mm rods that are completelly out of tolerance.

That one of the bom from aliexpress has H4 tolerance, -0.003 (7.997mm), the one of Europe location has H5 tolerance even if the seller says H6, bought and measured and has -0.005 (7.995mm)

The rod needs to be hardened to avoid the wear.

#### 2.1.5 Hotend

We don't support the Mini hotend, it are prone to heatcreep, because the lack of real heatbreak, also have a very low flow rate. You have some mounts for these toolhead.

The bang for buck option is the TZ-V6 2.0, the 2.0 version have M6 thread and you can fit V6 standard nozzles. With good non-cht noozle you can have 22-23mm3/s flow rate all-aroud and peak 25mm3/s for low density infills. This is about 280-350mm/s printing speed.

The TZ-V6 2.0 works very good with MMU.

## 3. Things to do

1. Read the BOM
2. Buy the parts
3. Use the ProosaXY step file to check assembly, read on discord the buildlogs
4. Read the bed assembly doc, it's important
5. Read the 20T idler assembly doc, it's different from normal proosaXy
6. Read the Z axis assembly doc, the procedure is also on discord server
7. Read the flash buddy doc, requires an extra step to do
8. Read the display config doc, it's required to do the modifications on your klipper files to able the use of the OEM LCD, if you don't want to use you can skip and put the LCD of your preference or klipperscreen.
9. The klipper config doc explains the connections of the provided config files, and how to grab +24V and GND from stock buddy board.

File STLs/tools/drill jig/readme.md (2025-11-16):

#  Before printing the jig

## 1. Printer calibration

You need to compensate the XY shrink of your filament.

Check your printer calibration and filament calibration, every filament had shrinkage. Print a 100mm piece and measure when it's cool, put your measurements in filament XY compensation part.

The printed part needs to measure 130mm, if you don't make this your part eventually measure 128.5-129mm and the 80/60mm marks will be displaced 1-1.5mm.

You need to print the holder to ensure the extrusion it's flat when drilling!

## 2. Two versions available.

20GT version is weaker but maybe you have worn out 20GT pulleys.

The bearing version requires MR115 bearings, can work with one bearing, recommended 2 bearings, lasts forever :)

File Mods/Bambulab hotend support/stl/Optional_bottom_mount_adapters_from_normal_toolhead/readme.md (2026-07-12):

# Support for existing hotend mounts

We developed this hotend-bottom-mount adapters to fit on bambulab style x-carrier.



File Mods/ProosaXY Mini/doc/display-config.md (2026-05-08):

# ProosaXY MINI OEM LCD config

This is a small step-by-step guide to configure the Prusa Mini stock LCD on klipper.

Klipper doesn't support by default the screen, this is based on this [old fork](https://github.com/singh-gur/mini_klipper), the problem of these fork is no longer maintained, and you can't update klipper version because it breaks, the module itself is outdated and can't run on an actual mainsail installation because the different python versions, most of the code uses deprecated functions.

There was also a problem with cs_pin reservation with new klipper versions.

This is a complete rework, installing and configuring only the necesary, you can update klipper but you will need to apply these changes again, I tried to optimize the code a bit the screen runs a bit slow, but is usable.

## 1. Configuring the system

This guide is made using as a host a standard mainsail installation from raspberry pi.

We need to access via SSH to our mainsail installation

```bash
ssh -l user mainsailos.local
```

We need to install within the klippy-env of klipper some modules

```bash
source ~/klippy-env/bin/activate
pip install pillow st7789
deactivate
```

Now we are going to edit the following file ~/klipper/klippy/extras/display/display.py on two places.

We are going to add at the ending of the line of imports **st7789v**

```python
# This file may be distributed under the terms of the GNU GPLv3 license.
import logging, os, ast
from . import aip31068_spi, hd44780, hd44780_spi, st7920, uc1701, menu, st7789v

```

Locate this part, then add 'st7789v': st7789v.ST7789V like the code below, don't forget the comma at the end of aip31068_spi,

```python
LCD_chips = {
    'st7920': st7920.ST7920, 'emulated_st7920': st7920.EmulatedST7920,
    'hd44780': hd44780.HD44780, 'uc1701': uc1701.UC1701,
    'ssd1306': uc1701.SSD1306, 'sh1106': uc1701.SH1106,
    'hd44780_spi': hd44780_spi.hd44780_spi,
    'aip31068_spi':aip31068_spi.aip31068_spi,
    'st7789v': st7789v.ST7789V
}
```

Copy the following files to ~/klipper/klippy/extras/display/

* st7789v.py
* logo.py
* logo.png

This files are under config/display section.

## 2. Cool font

If you want a cool font to change the booring standard font you can copy the file font8x14.py of config/display section to the path ~/klipper/klippy/extras/display/, [original author.](https://github.com/Klipper3d/klipper/issues/1564#issuecomment-487075600)

<p style="text-align:center;">

</p>

## 3. Display wires need to be longer

You need to lengthen the cables by about 45-50cm, no problems with SPI communication.

<p style="text-align:center;">
 
</p>

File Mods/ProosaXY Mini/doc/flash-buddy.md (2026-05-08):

# Buddy board flash

**In order to use with klipper we need to flash klipper firmware on our Buddy board. But you can do straight because Prusa protected to write unsigned firmwares on his board. To do this you need to break the appendix seal of your board or removing a jumper depending of your version of board.**

[Flashing-custom-firmware-mini](https://help.prusa3d.com/article/flashing-custom-firmware-mini-mini_14https:/)

You can flash back with prusa software, but the appendix won't grow back.

This guide is made for MainsailOS.

## 1. Compile klipper firmware

SSH to your MainsailOS install and generate the config to compile

```bash
cd ~/klipper/
make menuconfig
```

Then input the following options:

* Check Enable extra low-level configuration options
* set Microcontroller Architecture to STMicroelectronics STM32F407
* Bootloader offset to 128KiB + 512 Byte offset
* set clock reference to 12Mhz Crystal
* Set Communication interface to USB (on PA11/PA12)

Then save and exit.

Disconnect everything of your Buddy board, leaving only the power button, the LCD, the PSU and the USB connected to our MainsailOS machine.

We now are going to put the board in DFU mode,you don't need to put the jumper, just short and power on the board, the LCD screen goes white instead to load the Prusa bootloader, if the board shows the prusa mini logo you aren't in DFU mode, the LCD screen needs to be white.



When you are in DFU mode now list the USB devices to check the usb ID.

```bash
lsusb
....
....
Bus 001 Device 010: ID 0483:df11 STMicroelectronics STM Device in DFU Mode
....
....

```
If you don't see this, check your USB connection.

Now we need to flash the board with new firmware, but you cant with the dfu-utils available within this version of MainsailOS/Debian because are too new, and you can't downgrade via package, you need to download the dfu-utils-0.9 source code and compile, we need to remove first the actual dfu-utils version if installed.

```bash
sudo apt remove dfu-util
sudo apt install build-essential libusb-1.0-0-dev pkg-config
curl https://dfu-util.sourceforge.net/releases/dfu-util-0.9.tar.gz --output dfu09.tar.gz
tar -xvf dfu09.tar.gz dfu-util-0.9/
cd dfu-util-0.9
./configure
make
sudo make install
dfu-util --version
```

If you struggle with this we uploaded the dfu-util-0.9 compiled for this OS. Check doc/config/dfu-util on this repo.

With the correct version of dfu-util on our system we can flash now

```bash
sudo dfu-util -a 0 -D ~/klipper/out/klipper.bin
```

You will se some erros, it's okay. Now reset the board and check again the usb devices.

```bash
lsusb
...
...
Bus 001 Device 005: ID 1d50:614e OpenMoko, Inc. stm32f407xx
...
...
```
You will see now the buddy board correctly and now you can see the device available for serial communication.

```bash
ls /dev/serial/by-id/
usb-Klipper_stm32f407xx_56003A001150315239353820-if00
```
Congratulations you have now your buddy board with klipper firmware.

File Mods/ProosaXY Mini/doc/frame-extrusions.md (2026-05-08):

# ProosaXY MINI Frame extrusions

This document is recycled from ProosaXY, some extrusions are not at correct scale. The extrusions of proosa mini are the same types/letters but some extrusions differ on lenght

| Extrusion | Lenght | Number | Notes |
| --- | --- | --- | --- |
| A | 373 | 4 | |
| B | 310 | 2 | |
| C | 340 | 2 | You may want to make a hole at 45mm to have a hole to remove the motor mounts without remove an extrusion. |
| D | 270 | 3 | |
| E | 323 | 2 | |
| F | 340 | 2 | |
| G | 320 | 2 | |
| H | 180 | 2 | |
| I | 185 | 2 | This extrusion can be 200mm if you want to save some money on cuts. But you need to take in consideration for the holes |







## Extrusion C Hole



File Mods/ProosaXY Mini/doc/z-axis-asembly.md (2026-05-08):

# ProosaXY MINI Z-axis assembly

The procedure it's very similar as normal ProosaXY but with different z-rod-mount-aligner, you can do this without the aligner, the distance from the extrusion to the z-rod-bottom/top-mounts are 48mm.

## 1. Procedure

Build the frame and put the feet.



Then you need to put the printer upside down and use the z-rod-mount-aligner on LEFT mounts, thats one that have this shape, and thigthen.



Then do the same on right side using the Z-rod-mount-aligner.

When the front bottom/top rod mounts are thigthened you need to push the bed to the lowest position and thigthen the lower back rod mounts, then raise the bed to the top position and thigthen the top rod mounts.

If you done that you notice the bed will move freely up/down to the maximum positions. If one bearing doesn't reach their max range positions you may have a misaligned mounts. (check the video)

<p style="text-align:center;">

</p>

Then put the Z motors in, move the bed to the lowest position and tigthen the z motor mount screws.

Use your hand to rotate the z motor to move the bed up/down, make sure there are no binding or leadscrew mis-align. Repeat the align if needed.

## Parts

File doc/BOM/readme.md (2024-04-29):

# Bill of materials

## New BOM are moved to google doc [Click here](https://docs.google.com/spreadsheets/d/1j1bnA8rNjDqpTVEdiqrsRlNeggI6PYRAoSBm1F8bvCs/edit?usp=sharing)

## Openbeta kit are available here : [Fabreeko store](https://www.fabreeko.com/products/proosa-xy-conversion-for-mk3s-to-core-xy-by-snakeoilxy-open-beta)

- Last update : 2023/07/11
- There are 2 parts of the BOM. The requirement parts and option parts. 
- You can go with just requirement parts and keep the cost as low as possibe(about $100) or go a little fancy upgrade options parts(about $250 total).
- ~~I will try to work with vendors to make upgrade kit if the demands are high enough.~~ Frame kit will be made :)
- Fasteners are auto generated from the assembly CAD. If you spot any problem, please report in our discord.

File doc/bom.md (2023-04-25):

# Bill of materials (work in progress)

__*This BOM is still a work in progress.__

- There are 2 parts of the BOM. The requirement parts and option parts. 
- You can go with just requirement parts and keep the cost as low as possibe(about $100) or go a little fancy upgrade options parts(about $250 total).
- I will try to work with vendors to make upgrade kit if the demands are high enough.

## Requirement part

<table>
    <thead>
        <tr>
            <th>Item</th>
            <th>Quantity</th>
            <th>link</th>
            <th>Description</th>
            <th>Other</th>
        </tr>
    </thead>
    <tbody>
        <tr>
            <td>Frame</td>
            <td>1 set </td>
            <td></td>
            <td>Not available yet</td>
            <td></td>
        </tr>
        <tr>
            <td>F623RS bearing</td>
            <td>40pcs (4 packs)</td>
            <td><a href="https://s.click.aliexpress.com/e/_Dm4ZIwZ" rel="nofollow">Aliexpress</a></td>
            <td></td>
            <td></td>
        </tr>
        <tr>
            <td>Washer</td>
            <td>1 pack</td>
            <td><a href="https://s.click.aliexpress.com/e/_Dkq37S5" rel="nofollow">Aliexpress</a></td>
            <td>3x5x0.5 mm</td>
            <td></td>
        </tr>
        <tr>
            <td>M5 T-nut</td>
            <td>100pcs (1 pack)</td>
            <td><a href="https://s.click.aliexpress.com/e/_DkUMXQd" rel="nofollow">Aliexpress</a></td>
            <td></td>
            <td></td>
        </tr>
        <tr>
            <td>M3 heatset thread insert</td>
            <td>100pcs (1 pack)</td>
            <td><a href="https://s.click.aliexpress.com/e/_Ad1n92" rel="nofollow">Aliexpress</a></td>
            <td>M3 X D4.2 X L4.0</td>
            <td></td>
        </tr>
        <tr>
            <td>2GT belt</td>
            <td>???</td>
            <td></td>
            <td>Total length is not caculated yet</td>
            <td></td>
        </tr>
        <tr>
            <td>BMG Main Shaft Assembly</td>
            <td>1</td>
            <td><a href="https://www.bondtech.se/product/shaft-assembly/" rel="nofollow">Bondtech</a></td>
            <td>BMG plastic gear</td>
            <td></td>
        </tr>
        <tr>
            <td>Bearing for BMG shaft</td>
            <td>2</td>
            <td><a href="https://www.bondtech.se/product/ballbearing-5x8x2-5/" rel="nofollow">Bondtech</a></td>
            <td>BMG plastic gear</td>
            <td></td>
        </tr>
        <tr>
            <td>New Z motor</td>
            <td>1</td>
            <td><a href="https://s.click.aliexpress.com/e/_DF5e9Ol" rel="nofollow">Aliexpress</a></td>
            <td>Round nema14 17mm thick</td>
            <td></td>
        </tr>
    <tbody>
</table>

## Option parts(part numbers are not decided yet)

<table>
    <thead>
        <tr>
            <th>Item</th>
            <th>Quantity</th>
            <th>link</th>
            <th>Description</th>
            <th>Other</th>
        </tr>
    </thead>
    <tbody>
        <tr>
            <td>32 bit controller board</td>
            <td>1</td>
            <td></td>
            <td>Board with 5 drivers support(for 2Z axis build) or 6 drivers support(for 3Z axis build)</td>
            <td></td>
        </tr>
        <tr>
            <td>New XY motors</td>
            <td>2</td>
            <td></td>
            <td>The stock Prusa motor have very high inductance(13mH) make it not suitable for high speed application.</td>
            <td></td>
        </tr>
        <tr>
            <td>Extra 3rd Z motor(optional)</td>
            <td>1</td>
            <td></td>
            <td>OPTIONAL</td>
            <td></td>
        </tr>
        <tr>
            <td>AUX fan</td>
            <td>1</td>
            <td></td>
            <td></td>
            <td></td>
        </tr>
        <tr>
            <td>Hotend(optional)</td>
            <td>1</td>
            <td></td>
            <td>OPTIONAL. V6 will be support by default. Other hotends support will be added later.</td>
            <td></td>
        </tr>
    <tbody>
</table>

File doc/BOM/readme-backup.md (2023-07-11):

# Bill of materials (work in progress)

__*This BOM is still a work in progress.__

- There are 2 parts of the BOM. The requirement parts and option parts. 
- You can go with just requirement parts and keep the cost as low as possibe(about $100) or go a little fancy upgrade options parts(about $250 total).
- ~~I will try to work with vendors to make upgrade kit if the demands are high enough.~~ Frame kit will be made :)

## Requirement part

<table>
    <thead>
        <tr>
            <th>Item</th>
            <th>Quantity</th>
            <th>link</th>
            <th>Description</th>
            <th>Other</th>
        </tr>
    </thead>
    <tbody>
        <tr>
            <td>Frame</td>
            <td>1 set </td>
            <td></td>
            <td>Check Frame BOM(https://github.com/SnakeOilXY/ProosaXY/blob/master/doc/BOM/bom-frame.md)</td>
            <td></td>
        </tr>
        <tr>
            <td>F623RS bearing</td>
            <td>30pcs (3 packs)</td>
            <td><a href="https://s.click.aliexpress.com/e/_Dm4ZIwZ" rel="nofollow">Aliexpress</a></td>
            <td></td>
            <td></td>
        </tr>
        <tr>
            <td>Washer</td>
            <td>1 pack</td>
            <td><a href="https://s.click.aliexpress.com/e/_Dkq37S5" rel="nofollow">Aliexpress</a></td>
            <td>3x5x0.5 mm</td>
            <td></td>
        </tr>
        <tr>
            <td>2GT 16T idler 3mm bore</td>
            <td>2</td>
            <td><a href="https://s.click.aliexpress.com/e/_DFCSOgZ" rel="nofollow">Aliexpress</a></td>
            <td>Max height 8.5mm</td>
            <td></td>
        </tr>
        <tr>
            <td>M5 T-nut</td>
            <td>100pcs (1 pack)</td>
            <td><a href="https://s.click.aliexpress.com/e/_DkUMXQd" rel="nofollow">Aliexpress</a></td>
            <td></td>
            <td></td>
        </tr>
        <tr>
            <td>M3 heatset thread insert</td>
            <td>100pcs (1 pack)</td>
            <td><a href="https://s.click.aliexpress.com/e/_Ad1n92" rel="nofollow">Aliexpress</a></td>
            <td>M3 X D4.2 X L4.0</td>
            <td></td>
        </tr>
        <tr>
            <td>2GT belt 6mm wide</td>
            <td>4m</td>
            <td><a href="https://s.click.aliexpress.com/e/_DemEEAz" rel="nofollow">Aliexpress</a> or <a href="">E3D</a></td>
            <td></td>
            <td></td>
        </tr>
        <tr>
            <td>Hardware for Sherpa mini extruder</td>
            <td>1</td>
            <td><a href="https://s.click.aliexpress.com/e/_DDTsgzn" rel="nofollow">Full kit</a> or <a href="https://s.click.aliexpress.com/e/_DDMmLS9" rel="nofollow">Hardware only</a></td>
            <td>Both 17mm and 20mm version of nema14 motor will fit. 20mm version run cooler, but 17mm version max speed is a little higher.</td>
            <td>(body can be printed with ABS or filament with higher transition temperature)</td>
        </tr>
        <tr>
            <td>3rd Z motor (17hs3401s T8x8-310MM)</td>
            <td>1</td>
            <td><a href="https://s.click.aliexpress.com/e/_DBeGMNb" rel="nofollow">Aliexpress</a></td>
            <td>Will need to be cut to the right length.</td>
            <td></td>
        </tr>
        <tr>
            <td>8mm linear shaft 300mm</td>
            <td>1</td>
            <td><a href="https://s.click.aliexpress.com/e/_DkQvhBL" rel="nofollow">Aliexpress</a></td>
            <td>Will need to be cut to the right length.</td>
            <td></td>
        </tr>
        <tr>
            <td>MR115ZZ bearing</td>
            <td>2</td>
            <td><a href="https://s.click.aliexpress.com/e/_DCf9wSz" rel="nofollow">Aliexpress</a></td>
            <td></td>
            <td></td>
        </tr>
        <tr>
            <td>New POM T8 nut(lead 8mm)</td>
            <td>3</td>
            <td><a href="https://s.click.aliexpress.com/e/_DmUKgsv" rel="nofollow">Aliexpress</a></td>
            <td>Get standard diameter 22mm type. Old POM nuts are big and won't fit.</td>
            <td></td>
        </tr>
        <tr>
            <td>Rubber feet</td>
            <td>4pcs (1set)</td>
            <td><a href="https://s.click.aliexpress.com/e/_DB4UmaV" rel="nofollow">Aliexpress</a></td>
            <td>TPU printed version also available</td>
            <td></td>
        </tr>
        <tr>
            <td>2GT 20t 6mm pulley</td>
            <td>2</td>
            <td><a href="https://s.click.aliexpress.com/e/_DDZ5nYV" rel="nofollow">Aliexpress</a> or <a href="https://e3d-online.com/products/gates-belts-pulleys-and-idlers">E3D</a></td>
            <td></td>
            <td></td>
        </tr>
        <tr>
            <td>Din rail 329mm</td>
            <td>2</td>
            <td></td>
            <td></td>
            <td></td>
        </tr>
        <tr>
            <td>Din rail 430mm</td>
            <td>1</td>
            <td></td>
            <td></td>
            <td></td>
        </tr>
    <tbody>
</table>

## Option parts(highly recommended)

<table>
    <thead>
        <tr>
            <th>Item</th>
            <th>Quantity</th>
            <th>link</th>
            <th>Description</th>
            <th>Other</th>
        </tr>
    </thead>
    <tbody>
        <tr>
            <td>32 bit controller board</td>
            <td>1</td>
            <td></td>
            <td>Board with 5 drivers support(for 2Z axis build) or 6 drivers support(for 3Z axis build)</td>
            <td></td>
        </tr>
        <tr>
            <td>New XY motors (E3D High Torque Motor)</td>
            <td>2</td>
            <td><a href="https://e3d-online.com/products/motors" rel="nofollow">E3D</a></td>
            <td>The stock Prusa motor have very high inductance(13mH) make it not suitable for high speed application.</td>
            <td></td>
        </tr>
        <tr>
            <td>AUX fan (1232 blower)</td>
            <td>1</td>
            <td><a href="https://s.click.aliexpress.com/e/_DlIPXGz" rel="nofollow">Aliexpress</a></td>
            <td></td>
            <td></td>
        </tr>
        <tr>
            <td>Hotend(optional)</td>
            <td>1</td>
            <td></td>
            <td>OPTIONAL. Dragon, V6 and any other hotend have same mounting method are supported.</td>
            <td></td>
        </tr>
    <tbody>
</table>

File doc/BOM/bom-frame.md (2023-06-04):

# Frame BOM

## 1. Extrusions

- For extrusion profiles, drill hole size and position, check [extrusion drawing](../frame/frame-extrusion-drawing.pdf).
- You can source and drilling and tapping the frame your self, or wait for our official frame kit(will be release soon).

<table>
    <thead>
        <tr>
            <th>Item</th>
            <th>Quantity</th>
            <th>link</th>
            <th>Description</th>
            <th>Other</th>
        </tr>
    </thead>
    <tbody>
        <tr>
            <td>400mm 2020 T-slot</td>
            <td>4</td>
            <td></td>
            <td></td>
            <td></td>
        </tr>
        <tr>
            <td>370mm 2020 T-slot</td>
            <td>2</td>
            <td></td>
            <td></td>
            <td></td>
        </tr>
        <tr>
            <td>350mm 2020 T-slot</td>
            <td>2</td>
            <td></td>
            <td></td>
            <td></td>
        </tr>
        <tr>
            <td>340mm 2020 T-slot</td>
            <td>4</td>
            <td></td>
            <td></td>
            <td></td>
        </tr>
        <tr>
            <td>330mm 2020 T-slot</td>
            <td>3</td>
            <td></td>
            <td></td>
            <td></td>
        </tr>
        <tr>
            <td>320mm 2020 T-slot</td>
            <td>2</td>
            <td></td>
            <td></td>
            <td></td>
        </tr>
        <tr>
            <td>240mm 1515 T-slot</td>
            <td>3</td>
            <td></td>
            <td></td>
            <td></td>
        </tr>
        <tr>
            <td>225mm 1515 T-slot</td>
            <td>2</td>
            <td></td>
            <td></td>
            <td></td>
        </tr>
    </tbody>
</table>

## 2. Corner brackets and frame fasteners

<table>
    <thead>
        <tr>
            <th>Item</th>
            <th>Quantity</th>
            <th>link</th>
            <th>Description</th>
            <th>Other</th>
        </tr>
    </thead>
    <tbody>
        <tr>
            <td>2020 corner bracket</td>
            <td>14</td>
            <td><a href="https://s.click.aliexpress.com/e/_DEHKeDj" rel="nofollow">Aliexpress</a></td>
            <td></td>
            <td></td>
        </tr>
        <tr>
            <td>1515 corner bracket</td>
            <td>6</td>
            <td><a href="https://s.click.aliexpress.com/e/_DC2gu6l" rel="nofollow">Aliexpress</a></td>
            <td></td>
            <td></td>
        </tr>
        <tr>
            <td>M5x10 button head bolt</td>
            <td>28</td>
            <td><a href="https://s.click.aliexpress.com/e/_Dm4fL8N" rel="nofollow">Aliexpress</a></td>
            <td></td>
            <td></td>
        </tr>
        <tr>
            <td>M5x12 low profile flat head bolt</td>
            <td>10</td>
            <td><a href="https://s.click.aliexpress.com/e/_DC4i4Kz" rel="nofollow">Aliexpress</a></td>
            <td>Standard button head also works</td>
            <td></td>
        </tr>
        <tr>
            <td>M5x16 button head bolt</td>
            <td>26</td>
            <td><a href="https://s.click.aliexpress.com/e/_Dm4fL8N" rel="nofollow">Aliexpress</a></td>
            <td></td>
            <td></td>
        </tr>
        <tr>
            <td>M5 washer(M5x10x0.5)</td>
            <td>38</td>
            <td><a href="https://s.click.aliexpress.com/e/_DmNX0iV" rel="nofollow">Aliexpress</a></td>
            <td>M5x12 also works</td>
            <td></td>
        </tr>
        <tr>
            <td>M5 spring washer</td>
            <td>28</td>
            <td><a href="https://s.click.aliexpress.com/e/_DBbTiN3" rel="nofollow">Aliexpress</a></td>
            <td></td>
            <td></td>
        </tr>
        <tr>
            <td>M5 T-slot nut</td>
            <td>36</td>
            <td><a href="https://s.click.aliexpress.com/e/_DlTb4Q9" rel="nofollow">Aliexpress</a></td>
            <td></td>
            <td></td>
        </tr>
        <tr>
            <td>M6x30 bolt</td>
            <td>4</td>
            <td></td>
            <td>For mounting rubber feet</td>
            <td></td>
        </tr>
        <tr>
            <td>M6 hex nut</td>
            <td>4</td>
            <td></td>
            <td>For mounting rubber feet</td>
            <td></td>
        </tr>
        <tr>
            <td>Rubber feet</td>
            <td>1 set(4 pcs)</td>
            <td><a href="https://s.click.aliexpress.com/e/_DeKMEnf" rel="nofollow">Aliexpress</a></td>
            <td>TPU printed version also available.</td>
            <td></td>
        </tr>
    </tbody>
</table>

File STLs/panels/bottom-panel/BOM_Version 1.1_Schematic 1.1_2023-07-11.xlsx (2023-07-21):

No. | Quantity | Device | Designator | Footprint | Value | Manufacturer Part | Manufacturer | Supplier Part | Supplier
1 | 1 | CC0603KRX7R9BB104 | C1 | C0603 | 100nF | CC0603KRX7R9BB104 | YAGEO(国巨) | C14663 | LCSC
2 | 12 | CL10A106MA8NRNC | C2,C3,C5,C6,C7,C8,C9,C10,C11,C12,C25,C26 | C0603 | 10uF | CL10A106MA8NRNC | SAMSUNG(三星) | C96446 | LCSC
3 | 12 | CL31A476MPHNNNE | C13,C14,C15,C16,C17,C18,C19,C20,C21,C22,C23,C24 | C1206 | 47uF | CL31A476MPHNNNE | SAMSUNG(三星) | C96123 | LCSC
4 | 2 | 1.0T-4P卧贴 | CN1,CN2 | CONN-SMD_1.0T-4P |  | 1.0T-4P卧贴 | BOOMELE(博穆精密) | C145956 | LCSC
5 | 1 | PZ254V-11-04P | H1 | HDR-TH_4P-P2.54-V-M |  | PZ254V-11-04P | XFCN(兴飞) | C2691448 | LCSC
6 | 4 | KT-0603R | LED1,LED2,LED3,LED4 | LED0603-RD |  | KT-0603R |  | C2286 | LCSC
7 | 5 | MMBT5551_C2145 | Q1,Q2,Q3,Q4,Q5 | SOT-23-3_L2.9-W1.3-P1.90-LS2.4-BR |  | MMBT5551 | CJ(江苏长电/长晶) | C2145 | LCSC
8 | 15 | 0603WAF1002T5E | R1,R2,R3,R16,R17,R18,R19,R20,R21,R22,R23,R26,R27,R28,R29 | R0603 | 10kΩ | 0603WAF1002T5E | UNI-ROYAL(厚声) | C25804 | LCSC
9 | 8 | 0603WAF3002T5E | R4,R5,R6,R7,R8,R9,R10,R11 | R0603 | 30kΩ | 0603WAF3002T5E | UNI-ROYAL(厚声) | C22984 | LCSC
10 | 4 | 0603WAF6800T5E | R12,R13,R14,R15 | R0603 | 680Ω | 0603WAF6800T5E | UNI-ROYAL(厚声) | C23228 | LCSC
11 | 2 | 0603WAF6801T5E | R24,R25 | R0603 | 6.8kΩ | 0603WAF6801T5E | UNI-ROYAL(厚声) | C23212 | LCSC
12 | 5 | SRV05-4-P-T7_C85364 | TV1,TV2,TV3,TV4,TV5 | SOT-23-6_L2.9-W1.6-P0.95-LS2.8-BR |  | SRV05-4-P-T7 | PROTEK | C85364 | LCSC
13 | 1 | PCA9557PW,118 | U1 | TSSOP-16_L5.0-W4.4-P0.65-LS6.4-BL |  | PCA9557PW,118 | NXP(恩智浦) | C141380 | LCSC
14 | 1 | SL2.1A | U2 | SOP-16_L10.0-W3.9-P1.27-LS6.0-BL |  | SL2.1A | CoreChips(和芯润德) | C192893 | LCSC
15 | 5 | MT9700 | U3,U4,U5,U6,U7 | SOT-23-5_L3.0-W1.7-P0.95-LS2.8-BR |  | MT9700 | 西安航天民芯 | C89855 | LCSC
16 | 1 | BTC-MC5S-43 | USB1 | MICRO-USB-SMD_MICRO-USB-BTC-MC5S-43 |  | BTC-MC5S-43 | DGBZ(东莞博众) | C2908217 | LCSC
17 | 4 | AF 10.0 QT-ZB6.8 | USB2,USB3,USB4,USB5 | USB-A-SMD_AF-10.0-QT-ZB6.8 |  | AF 10.0 QT-ZB6.8 | SHOU HAN(首韩) | C456016 | LCSC
18 | 1 | X322512MSB4SI | X1 | OSC-SMD_4P-L3.2-W2.5-BL | 12MHz | X322512MSB4SI | YXC(扬兴晶振) | C9002 | LCSC

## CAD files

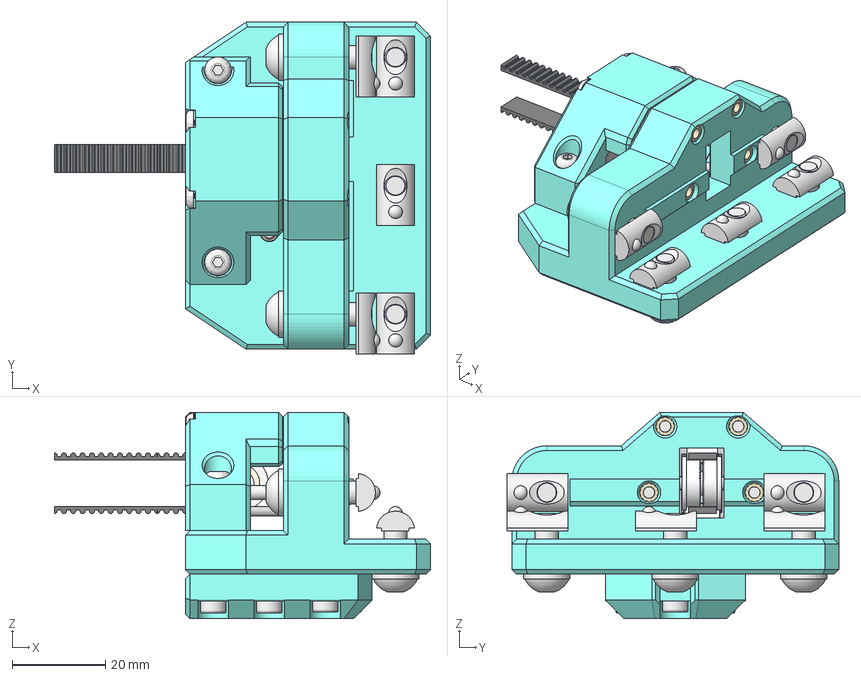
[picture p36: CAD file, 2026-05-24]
Mods/Front belt tensioners/src/front-belt-tensioner-10mm-rod-assembly.step
80.5 x 71.0 x 44.2 mm
y-rod-mount-cap002
flat washer narrow_am_B18.22M - Plain washer, 3 mm, narrow x 3
F623ZZ Flange Bearing x 2
VITE_TESTA_BOMBATA_ESAGONO_INCASSATO
M3x25-Screw048 x 2
VITE_TESTA_BOMBATA_ESAGONO_INCASSATO_1 x 2
VITE_TESTA_BOMBATA_ESAGONO_INCASSATO_2
M5x20-Screw040 x 2
M5x14-Screw016 x 3
M3x10-Screw082
M3x14-Screw089 x 6
Knurled Insert M3xH4 x 13
M5-Washer140 x 5
M2x30 dowel pin x 4
M3x16 dowel pin
FusionComponent x 2

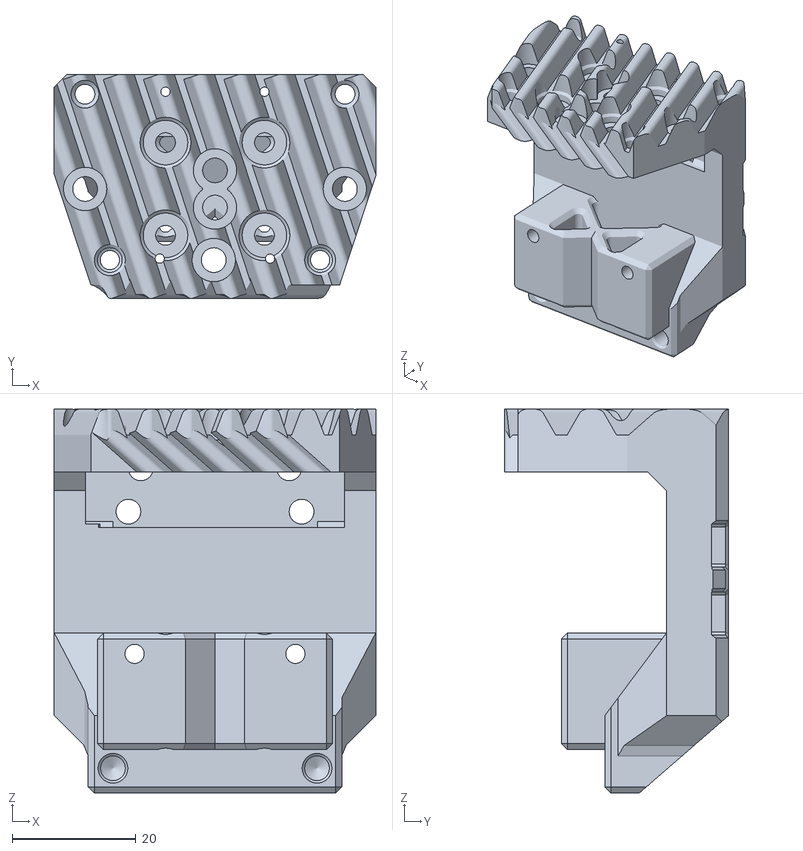
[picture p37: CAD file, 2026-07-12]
Mods/MGN9H X carrier/stl/1x_mgn9h_carrier_main_body_std.stl
52.0 x 36.2 x 62.1

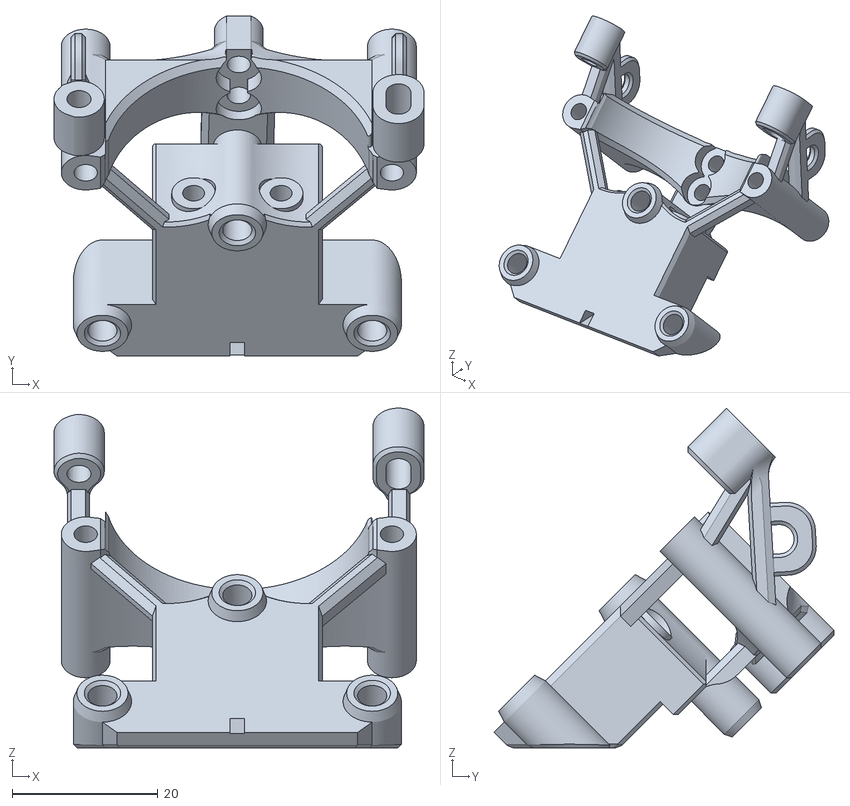
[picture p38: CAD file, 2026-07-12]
Mods/MGN9H X carrier/stl/x-carrier-motor-support(pick-one)/snakeoil_toolboard/1x_motor_support_snakeoil_toolboard_main.stl
50.8 x 46.6 x 46.6

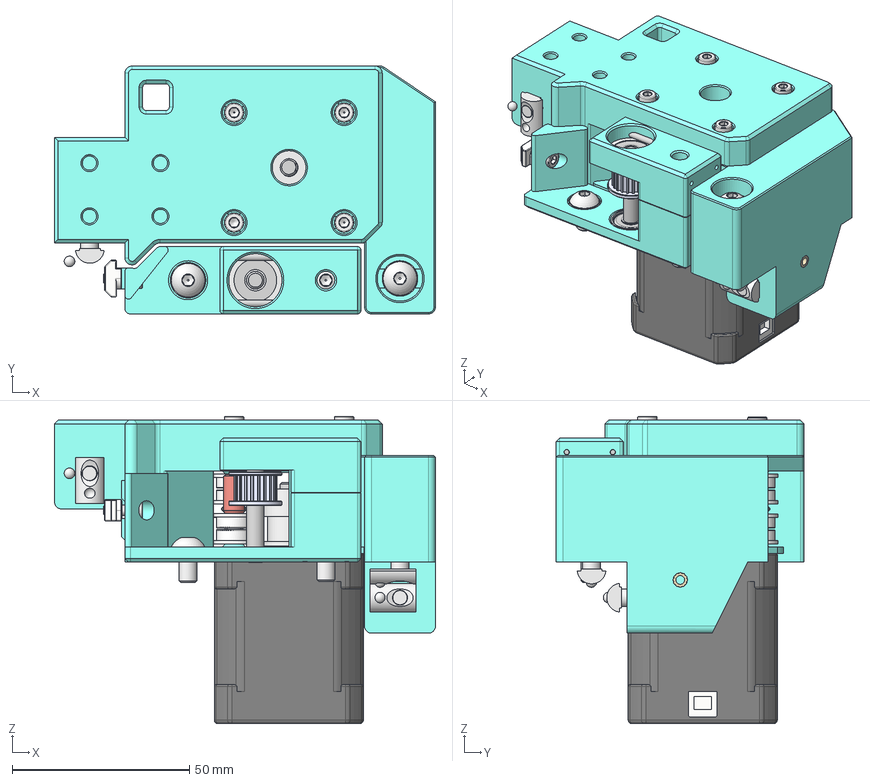
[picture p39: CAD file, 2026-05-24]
Mods/Rear Live idlers/src/rear-left-live-idler-assembly.step
107.4 x 69.9 x 86.6 mm
motor-mounter-cap001
motor-mounter-spacer002
motor-mounter-main001
MR115ZZ
20t-pulley001
NEMA17 Stepper_48mm
M3x40-Screw012 x 4
Knurled Insert M3xH4
F623ZZ Flange Bearing x 6
flat washer narrow_am_B18.22M - Plain washer, 3 mm, narrow x 2
short-spacer001
3x4x8.5 spacer v1(Simetría)
M5x30-Screw004 x 2
M5x20-Screw040
M5-Washer140 x 3
M5x20-Screw040_1
M5x10-Screw060
M3x8-Screw078
M3x20-Screw x 4
2020 - M3 T-Nut
Knurled Insert M3xH4_1 x 4
M5-Washer140_1 x 2
M2x30 dowel pin x 2
M5x30 dowel pin
rear-live-idler-top
rear-live-idler-bottom
rear-live-idler-bottom-support-for-print
F695 Bearing x 2
GT2 20T5B_dz2020
Espaciadores proosa live idlers

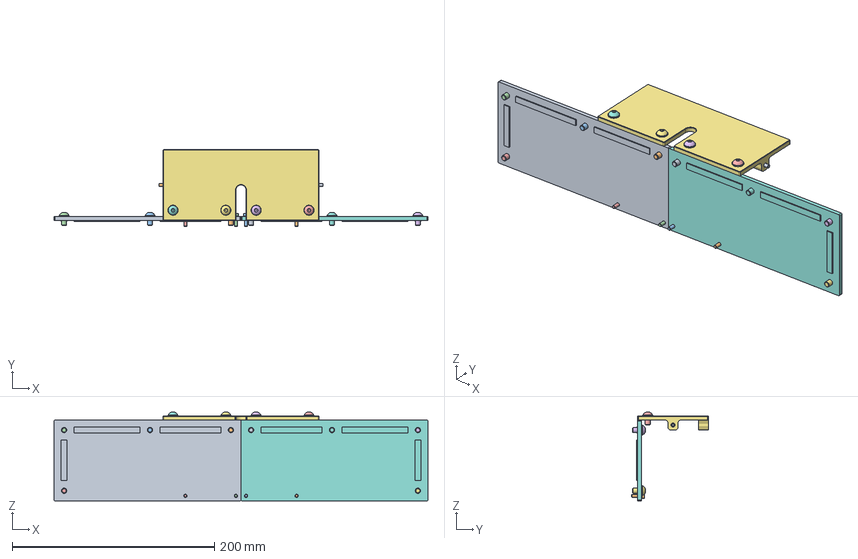
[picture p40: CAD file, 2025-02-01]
src/freecad/component-assembly/cable-panel-cover-assembly.FCStd
370.0 x 76.0 x 87.8 mm
M5-Washer
M5-Washer026
M5-Washer027
M5-Washer028
M5x10-Screw
M5x10-Screw026
M5x10-Screw027
M5x10-Screw028
M3x14-Screw
M3x14-Screw001
M3x5.74-Insert
M3x5.74-Insert010
M3x5.74-Insert011
M3x5.74-Insert012
cable-mount-cover002
back-panel-cover
back-panel-cover (Mirror #1)001
M3x10-Screw
M3x10-Screw009
M3x10-Screw010
M3x10-Screw011
M5-Washer029
M5-Washer030
M5-Washer031
M5-Washer032
M5-Washer033
M5-Washer034
M5-Washer035
M5-Washer036
M5x10-Screw029
M5x10-Screw030
M5x10-Screw031
M5x10-Screw032
M5x10-Screw033
M5x10-Screw034
M5x10-Screw035
M5x10-Screw036

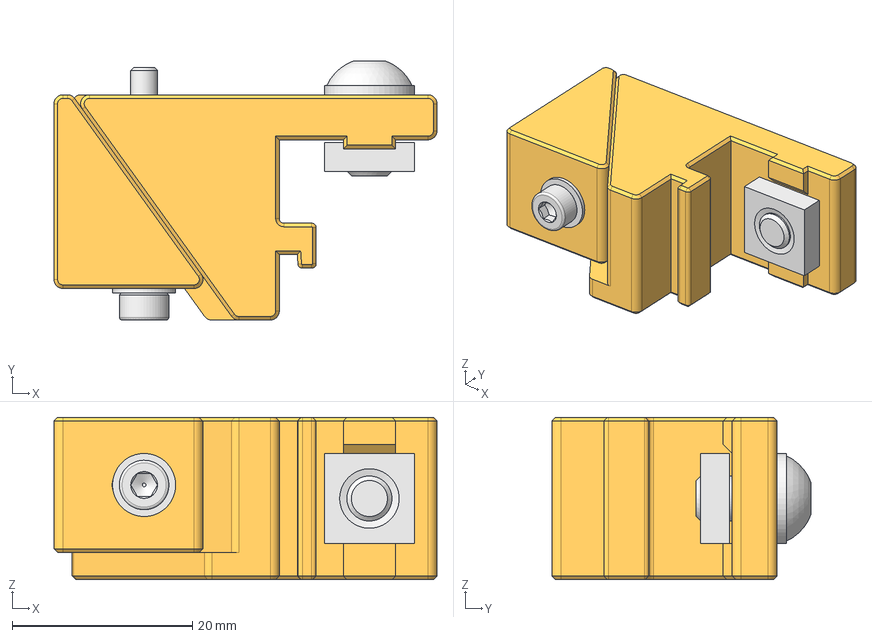
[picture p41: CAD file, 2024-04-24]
src/freecad/component-assembly/ab-motor-support-assembly.FCStd
42.5 x 28.8 x 18.0 mm
M5-Washer
M3-Washer
M5x10-Screw
M3x25-Screw
M6-Nut
M3x5.74-Insert
motor-support-body-left
motor-support-slider-left

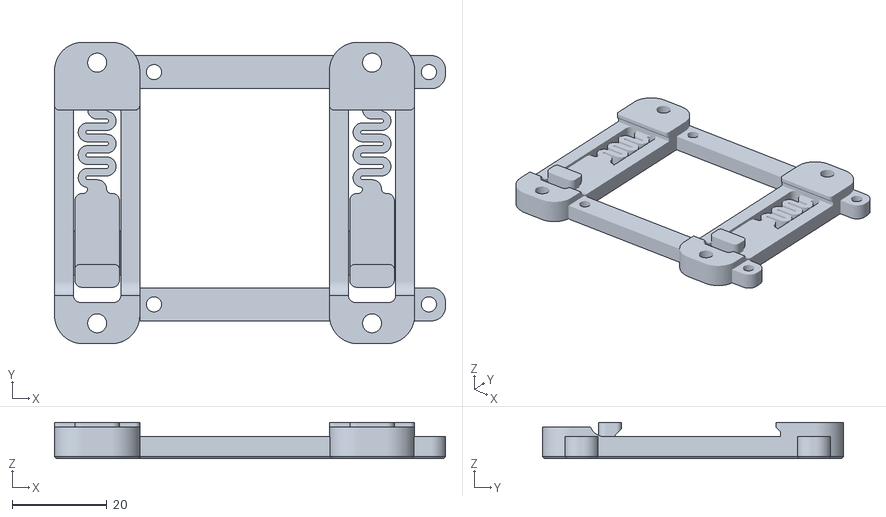
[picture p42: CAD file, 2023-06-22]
STLs/Other/DIN/raspberry-mounter/OPTIONAL_1x_raspberry-full-size-din-mounter.stl
82.5 x 63.6 x 7.60

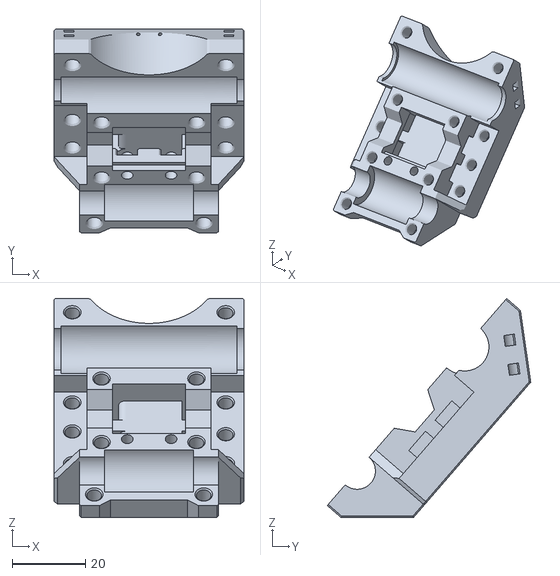
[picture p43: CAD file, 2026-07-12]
Mods/Bambulab hotend support/stl/1x_lm8uu_carrier_main_body_bambulab(pick_one).stl
52.0 x 55.7 x 60.0

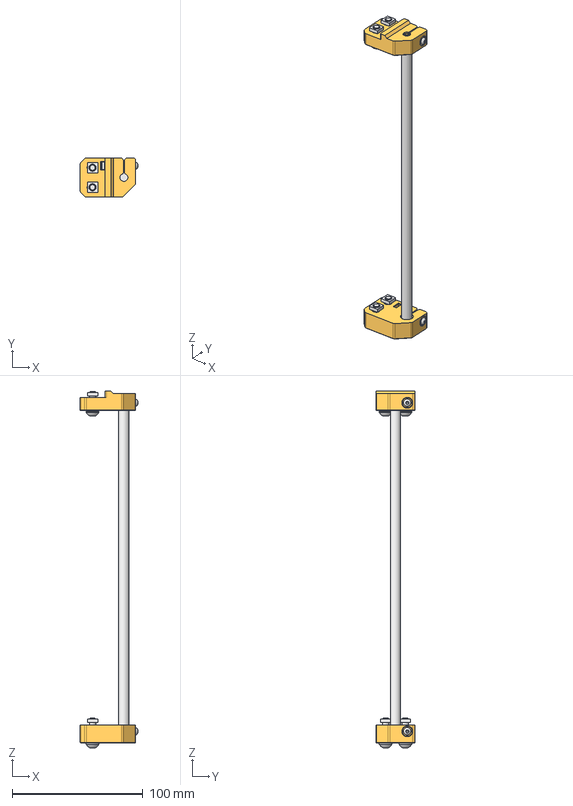
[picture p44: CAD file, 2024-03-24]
src/freecad/component-assembly/z-shaft-assembly.FCStd
44.1 x 30.0 x 272.8 mm
260mm-shaft
M5-Washer015
M5-Washer016
M5-Washer017
M5-Washer018
M5x16-Screw008
M5x16-Screw009
M5x20-Screw007
M5x20-Screw008
M5-Nut011
M5-Nut012
M5-Nut013
M5-Nut014
M3-Nut006
M3-Nut005
M3x25-Screw018
M3x25-Screw019
z-rod-bottom-mount-left-loose
z-rod-top-mount-left-loose
M3x25-Screw021
M3x25-Screw020

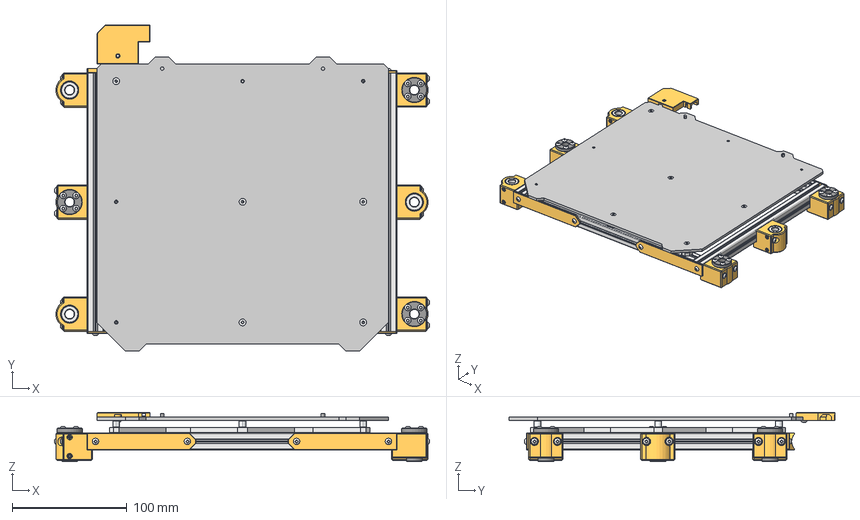
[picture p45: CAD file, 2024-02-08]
src/freecad/component-assembly/bed-assembly.FCStd
326.4 x 283.9 x 42.8 mm
M3x12-Screw
M3x12-Screw001
M3x12-Screw002
M3x12-Screw003
M3x18-Screw004
M3x18-Screw003
M3x18-Screw
M3x18-Screw001
M3x12-Screw004
MK52 Bed
6x6x3t spacer008
6x6x3t spacer003
6x6x3t spacer001
6x6x3t spacer006
6x6x3t spacer
6x6x3t spacer005
6x6x3t spacer004
6x6x3t spacer007
6x6x3t spacer002
bed-cable-cover
M3x6-Screw
M3-Nut
M3-Nut001
mk3-bed-frame
M3-Nut025
M3-Nut024
1515-225mm001
1515-240mm001
1515-225mm
1515-240mm
M3x10-Screw011
M3x10-Screw008
M3x10-Screw012
M3x10-Screw010
bed-cable-mounter
extrusion-cap
extrusion-cap001
extrusion-cap002
M3x10-Screw
M3x6-Screw002
M3x6-Screw003
M3x10-Screw001
M3x6-Screw006
M3x6-Screw004
M3x6-Screw005
M3x10-Screw002
M3-Nut003
M3-Nut004
M3-Nut005
M3-Nut006
bed-bearing-mounter
LM8UU
M3-HeatSet
M3-HeatSet001
M3-HeatSet002
M3-HeatSet003
M3x8-Screw
M3x8-Screw001
M3x8-Screw002
M3x8-Screw003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

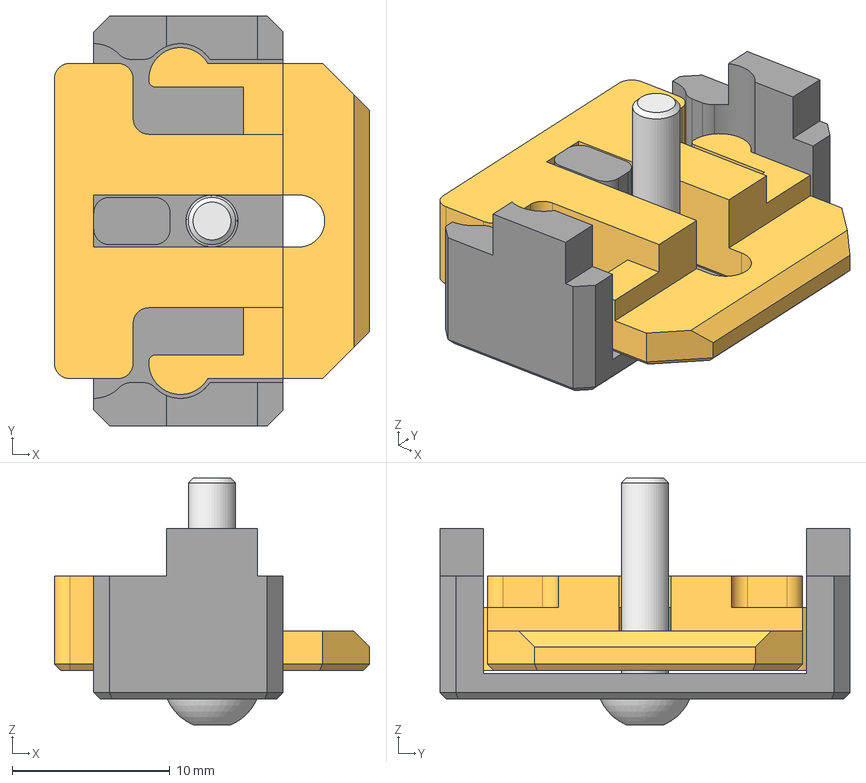
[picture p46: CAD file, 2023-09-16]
src/freecad/component-assembly/panel-clip-assembly.FCStd
20.0 x 26.0 x 15.7 mm
housing-m006
clip-m006
M3x14-Screw

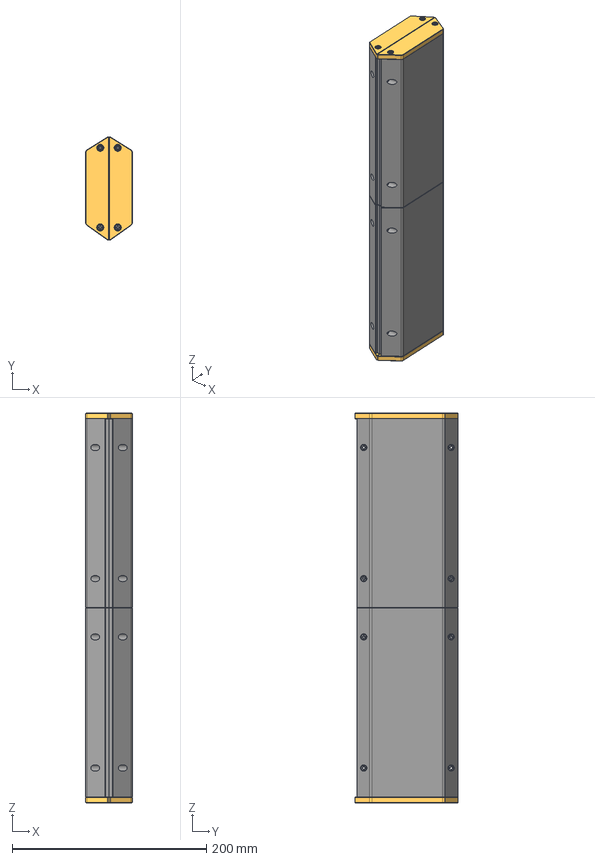
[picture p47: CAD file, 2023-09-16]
src/freecad/component-assembly/y-cover-assembly.FCStd
48.0 x 106.3 x 401.5 mm
y-cover-cap001 (Mirror #1)001
y-cover-body001
y-cover-cap
y-cover-body
M3x10-Screw
M3x10-Screw001
M3x10-Screw002
M3x10-Screw003
M3x10-Screw004
M3x10-Screw005
M3x10-Screw006
M3x10-Screw007
M3x8-Screw
M3x8-Screw004
M3x8-Screw002
M3x8-Screw003
y-cover-cap001 (Mirror #1)001 (Mirror #4)001
y-cover-body001 (Mirror #3)001
y-cover-cap (Mirror #2)001
y-cover-body (Mirror #1)001
M3x10-Screw008
M3x10-Screw009
M3x10-Screw010
M3x10-Screw011
M3x10-Screw012
M3x10-Screw013
M3x10-Screw014
M3x10-Screw015
M3x8-Screw009
M3x8-Screw010
M3x8-Screw007
M3x8-Screw008

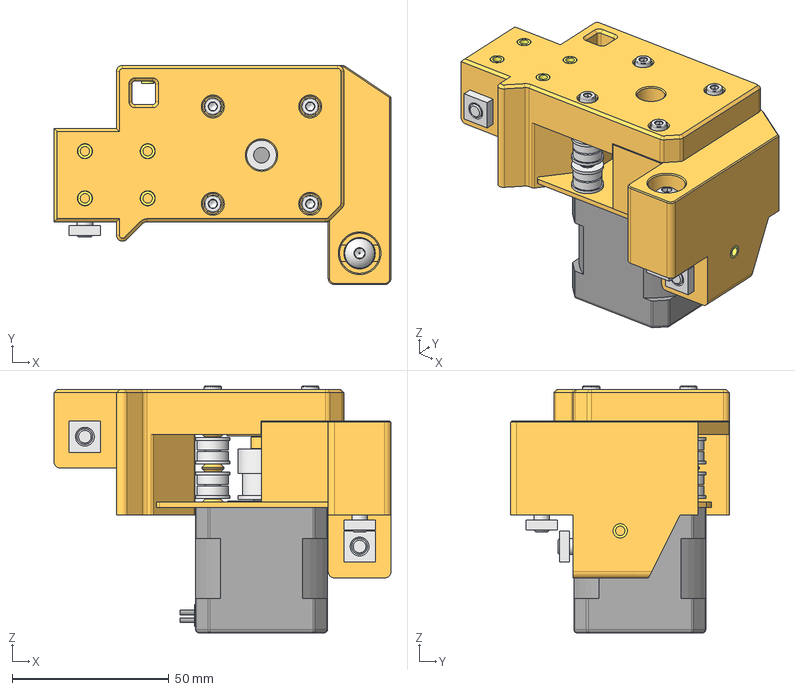
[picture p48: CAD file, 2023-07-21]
src/freecad/component-assembly/ab-motor-assembly.FCStd
107.3 x 69.9 x 78.6 mm
short-spacer002
short-spacer003
bearing-stack003
bearing-stack004
20t-pulley002
MR115ZZ001
bearing-stack005
x-motor
motor-mounter-spacer003 (Mirror #3)001
motor-mounter-main002 (Mirror #2)001
motor-mounter-cap002 (Mirror #1)001
motor-spacer001
M3x40-Screw008
M3x40-Screw009
M3x40-Screw010
M3x40-Screw011
M3-HeatSet006
M3-HeatSet007
M3-HeatSet008
M3-HeatSet009
M3-HeatSet010
M3-HeatSet011
M5-Washer006
M5-Washer007
M5-Washer005
M5x30-Screw002
M5x30-Screw003
M5x20-Screw002
M6-Nut003
M6-Nut004
M6-Nut005
bearing-stack007

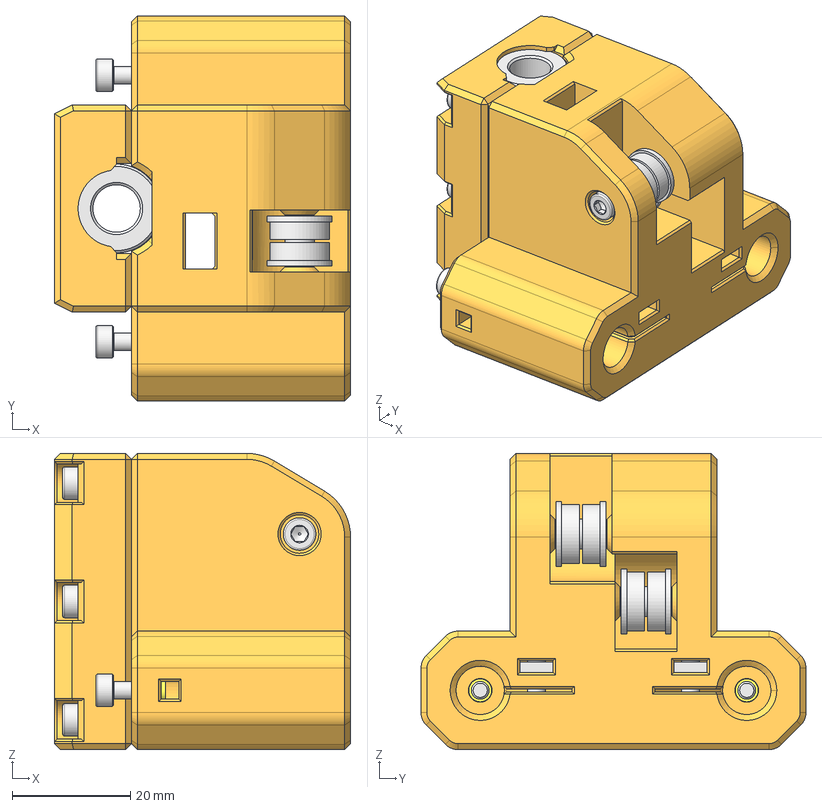
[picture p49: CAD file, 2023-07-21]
src/freecad/component-assembly/y-carrier-assembly.FCStd
50.0 x 65.0 x 50.0 mm
LM8UU001
LM8UU002
M3-HeatSet
M3-HeatSet001
M3-HeatSet002
M3-HeatSet003
M3-HeatSet004
M3-HeatSet005
M3-HeatSet006
M3-HeatSet007
M3-Nut
M3-Nut001
M3x14-Screw
M3x14-Screw008
M3x14-Screw009
M3x14-Screw010
M3x14-Screw011
M3x14-Screw012
M3x14-Screw013
M3x14-Screw014
M3x20-Screw
M3x8-Screw
M3x8-Screw001
bearing-stack
y-carrier-common002
y-carrier-cap002
M3x20-Screw001
bearing-stack001

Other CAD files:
Mods/Bambulab hotend support/stl/1x_mgn9h_carrier_main_body_bambulab(pick_one).stl
Mods/Front belt tensioners/src/front-belt-tensioner-8mm-rod-assembly.step
Mods/Rear Live idlers/src/rear-right-live-idler-assembly.step
src/freecad/component-assembly/back-panel-assembly.FCStd
Mods/Bambulab hotend support/stl/1x_bambulab_fan_pinda_support.stl
Mods/Bambulab hotend support/stl/1x_bambulab_printed_insulator.stl
Mods/Bambulab hotend support/stl/Optional_bottom_mount_adapters_from_normal_toolhead/1x_hotend-bottom-mount-TZ-BBL.stl
Mods/Bambulab hotend support/stl/Optional_bottom_mount_adapters_from_normal_toolhead/1x_hotend-bottom-mount-V6-BBL.stl
Mods/Bambulab hotend support/stl/Optional_bottom_mount_adapters_from_normal_toolhead/1x_hotend-bottom-mount-Volcano-BBL.stl
Mods/Front belt tensioners/stl/2x_front-tensioner-bearing-holder.stl
Mods/Front belt tensioners/stl/2x_front-tensioner-cap.stl
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

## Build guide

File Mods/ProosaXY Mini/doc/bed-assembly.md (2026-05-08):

# ProosaXY Mini bed assembly

## 1. Intro

Unlike the MK3S the bed frame on the mini doesn't have threaded holes for 9 screw assembly.

Instead it use standoffs and very small m3 counter sunk screws.

This is not very convinient if you want to print PETG or even ABS if you enclose the printer, because the bed will bend like a taco. Even if you don't want to print with high temperature bed, your bed frame could be warped because an accidental hit.

For that reason we will use the silicon mod to assemble the bed pcb to the frame and then to the extrusions.

## 2. Check the screws first

Te typical FHCS screws doesn't sit flat on MINI bed.

<p style="text-align:center;">
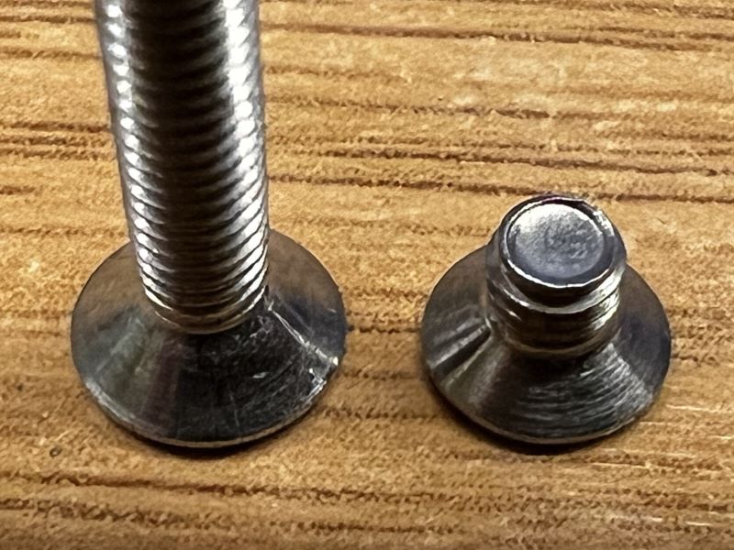
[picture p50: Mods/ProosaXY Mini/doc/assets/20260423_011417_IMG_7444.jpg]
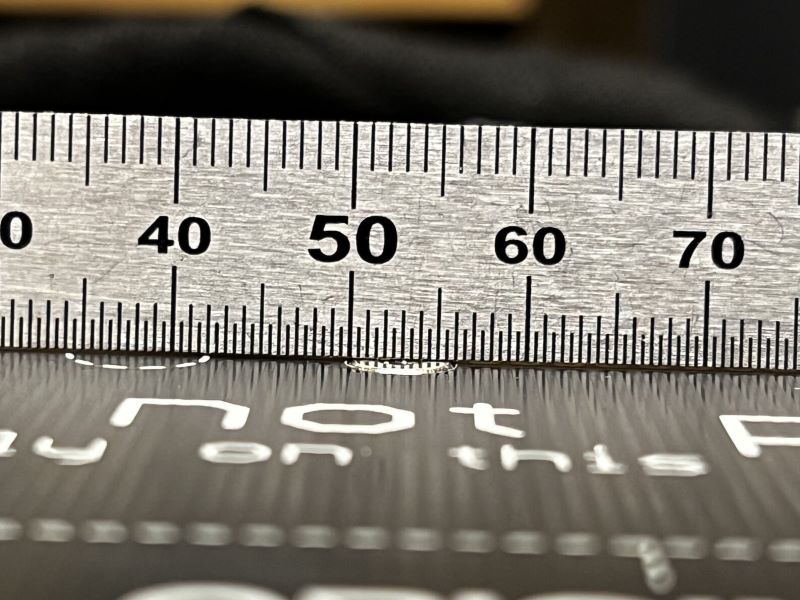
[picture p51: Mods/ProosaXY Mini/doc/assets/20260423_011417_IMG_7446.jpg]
 
</p>

You can use a drill and a file to sand down the screw on the top part and the circunference.

You can check on this photos the difference.

<p style="text-align:center;">
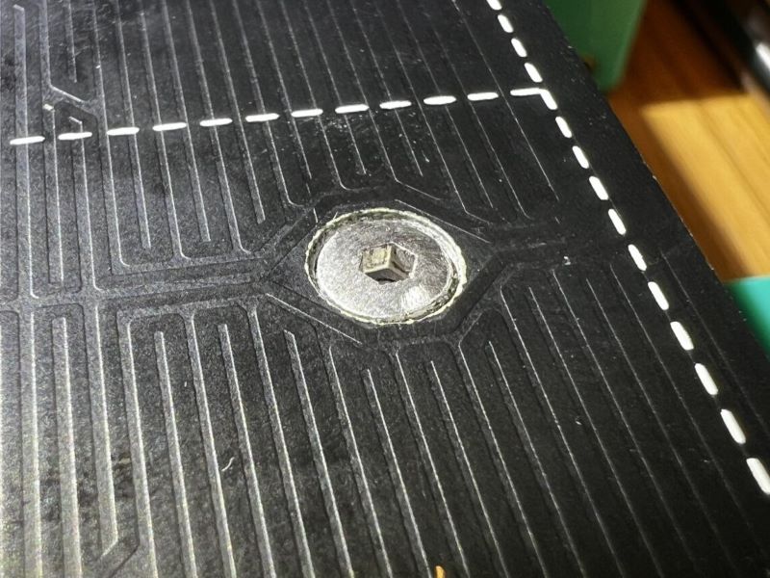
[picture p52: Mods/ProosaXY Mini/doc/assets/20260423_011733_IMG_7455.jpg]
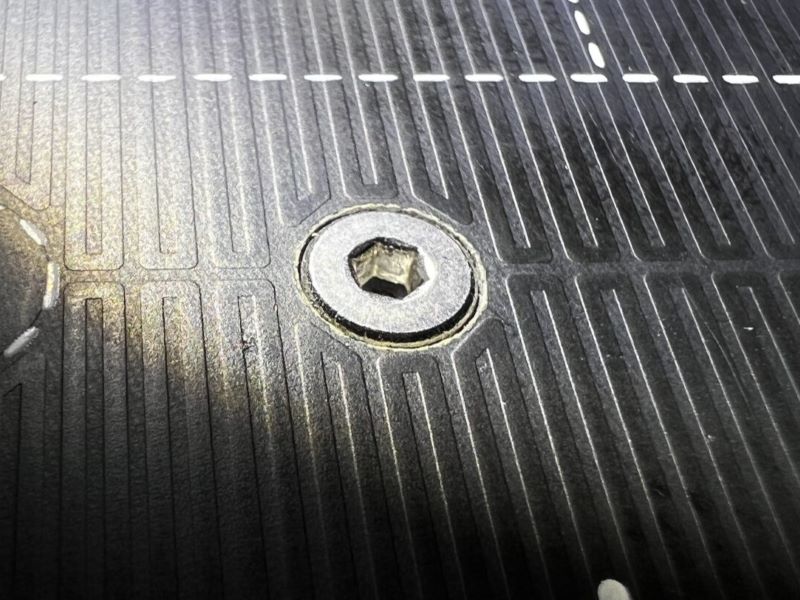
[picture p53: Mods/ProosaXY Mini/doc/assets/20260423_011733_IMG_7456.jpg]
 
</p>

### 2.1 Screw sizes, nuts and spacers

You need:

* x4 M3x25 FHCS for the corners
* x5 M3x18 FHCS for the rest
* x3 M3x10 BHCS/SHCS
* x5 nylock nuts
* x4 6x6x3 metal spacers, (the same of the MK3S bed)

## 3. Bed frame position

Assemble the frame and the pom nut holders/lm8uu holders.

The bed frame will be mounted on the far left side, leaving space on the right to able the nozzle go outside the bed.

<p style="text-align:center;">
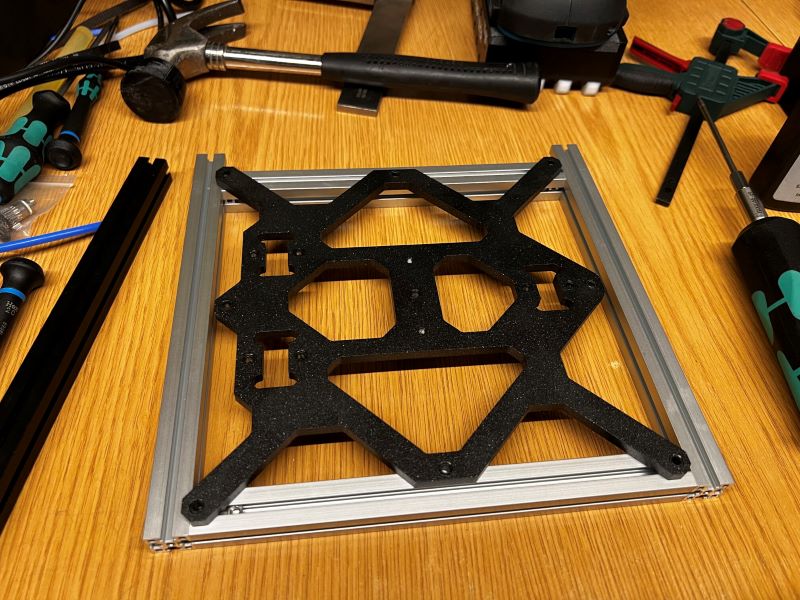
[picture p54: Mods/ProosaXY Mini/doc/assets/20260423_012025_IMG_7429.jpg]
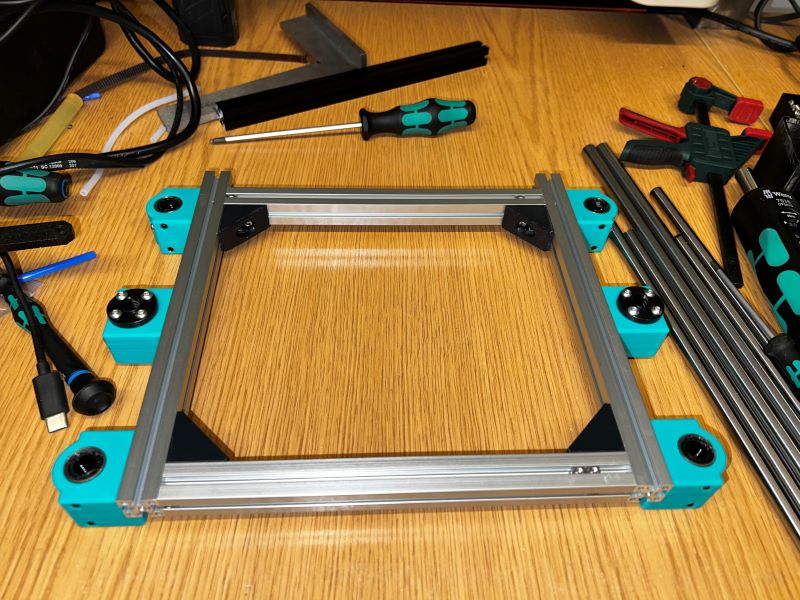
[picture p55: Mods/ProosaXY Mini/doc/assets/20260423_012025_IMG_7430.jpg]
 
</p>

## 4. Bed helper

This is not mandatory but it's 100% recommended, due this able to hold the nyloc nuts in place to adjust the silicon mod, and makes easy the installation on the extrusions without needing to hold by hand the bed spacers.

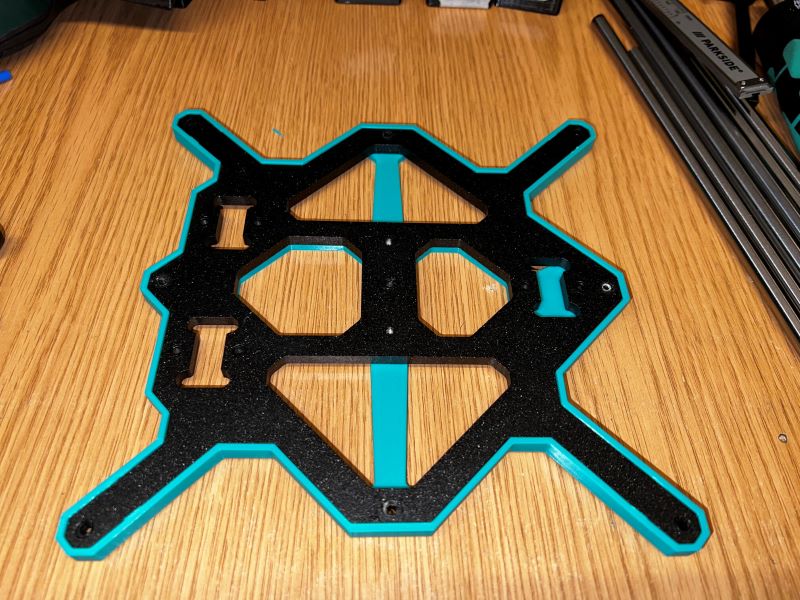
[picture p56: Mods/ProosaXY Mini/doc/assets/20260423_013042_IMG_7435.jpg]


Assemble like this photo, don't forget to put the silicon tubes before on each screw.

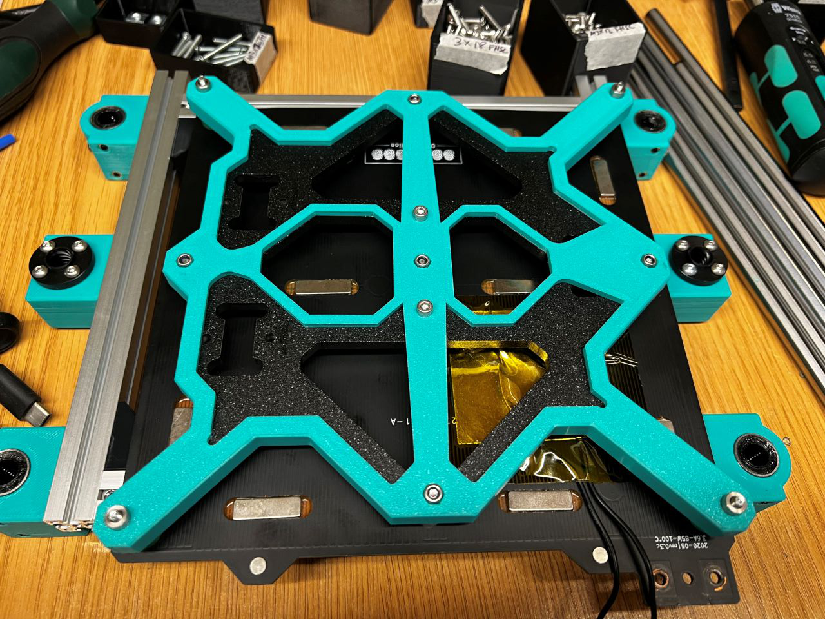
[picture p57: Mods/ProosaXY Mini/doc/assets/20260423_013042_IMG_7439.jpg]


With the bed helper this task is easy peasy.

<p style="text-align:center;">
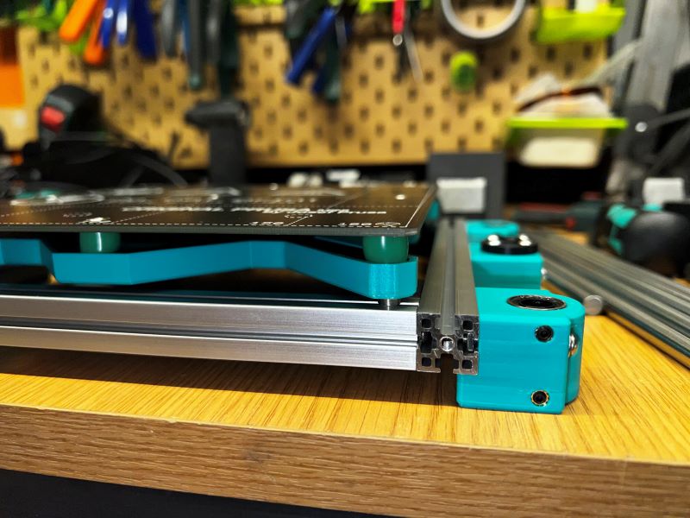
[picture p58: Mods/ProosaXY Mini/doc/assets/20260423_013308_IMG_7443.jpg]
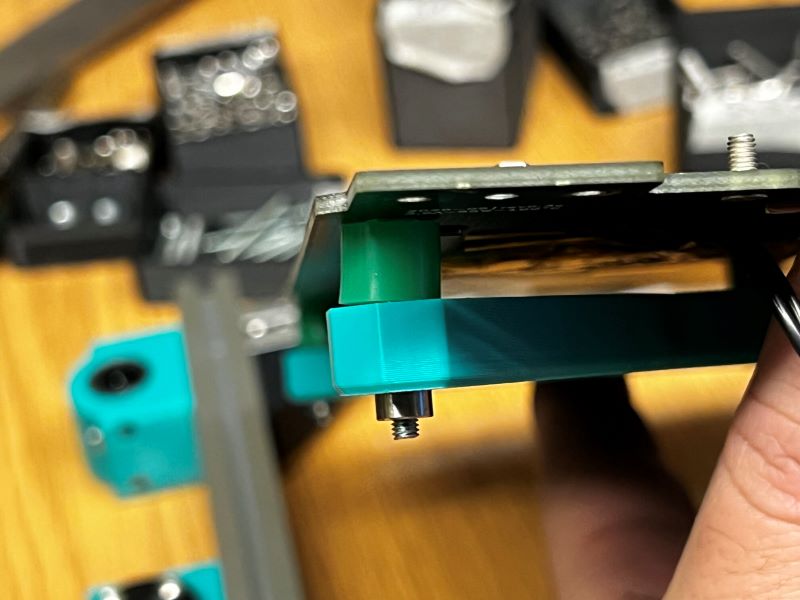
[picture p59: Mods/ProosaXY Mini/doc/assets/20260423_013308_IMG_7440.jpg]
 
</p>

You can use a ruler to eyeball adjust the bed, but you can adjust later.

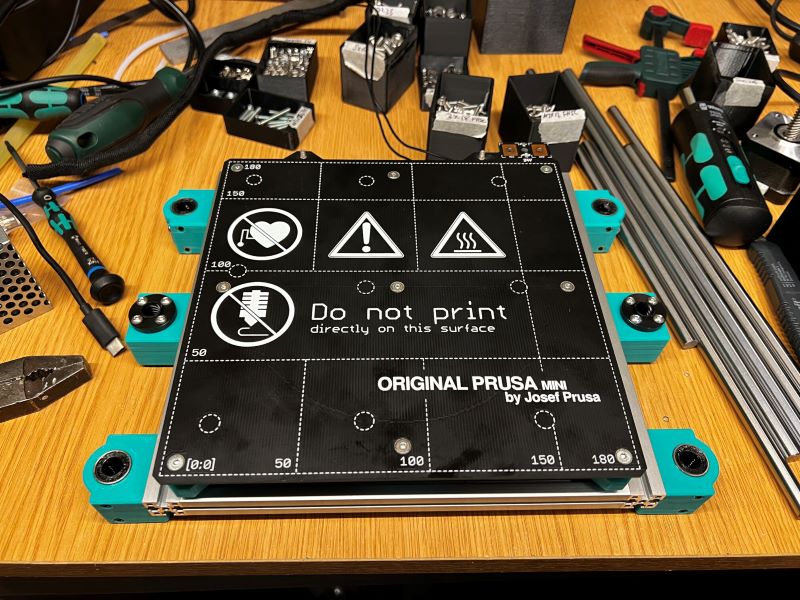
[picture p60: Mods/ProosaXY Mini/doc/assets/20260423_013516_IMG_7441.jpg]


## 5. Print surface stoppers

This screws that are used to hold the plate in place are too long and will scrub your print fan shroud, on MK3S it are 3.2mm tall, on mini are 4.2mm tall, you need to trim a bit with a file.

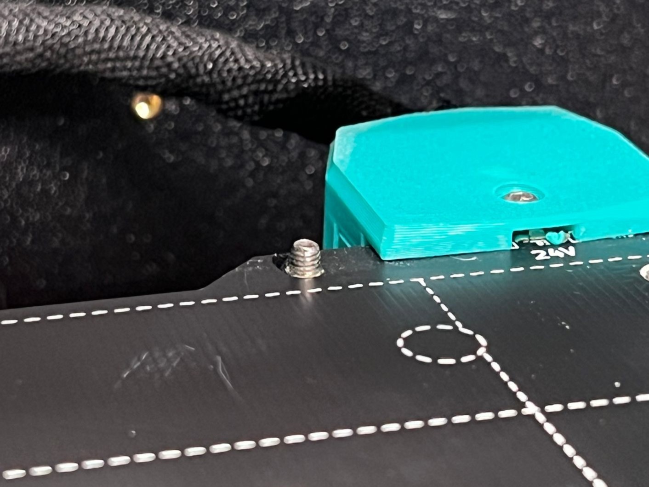
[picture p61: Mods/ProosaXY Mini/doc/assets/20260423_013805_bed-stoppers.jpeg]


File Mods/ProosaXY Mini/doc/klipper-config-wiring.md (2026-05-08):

# ProosaXY Mini klipper config

## Config

A base config is provided, is the config of the ProosaXY Mini #SP00F that have the following parts

* OMC HE19 2A steppers for A/B
* Hanspose TR8x8 leadscrew steppers for Z
* BTT EBB42 1.0 MCU
* Builtin toolhead filament sensor
* TZ-V6 2.0 Hotend with 48W heater

**This config is uploaded on config section.**

If you need some help you can reach us on discord ;)

## Wiring

Take in consideration that Buddy board uses 5V on all fans/sensors, if you want to use 12/24v fans you will need to plug on different MCU

To avoid the modification of PSU wires to have +24/GND you can take it from the buddy board, we recommend to do not use the standard switch to switch on/off the board, instead of that we recomend to put IEC socket and modify a standard PSU cable, with this you can power an LRS-25-5 :)

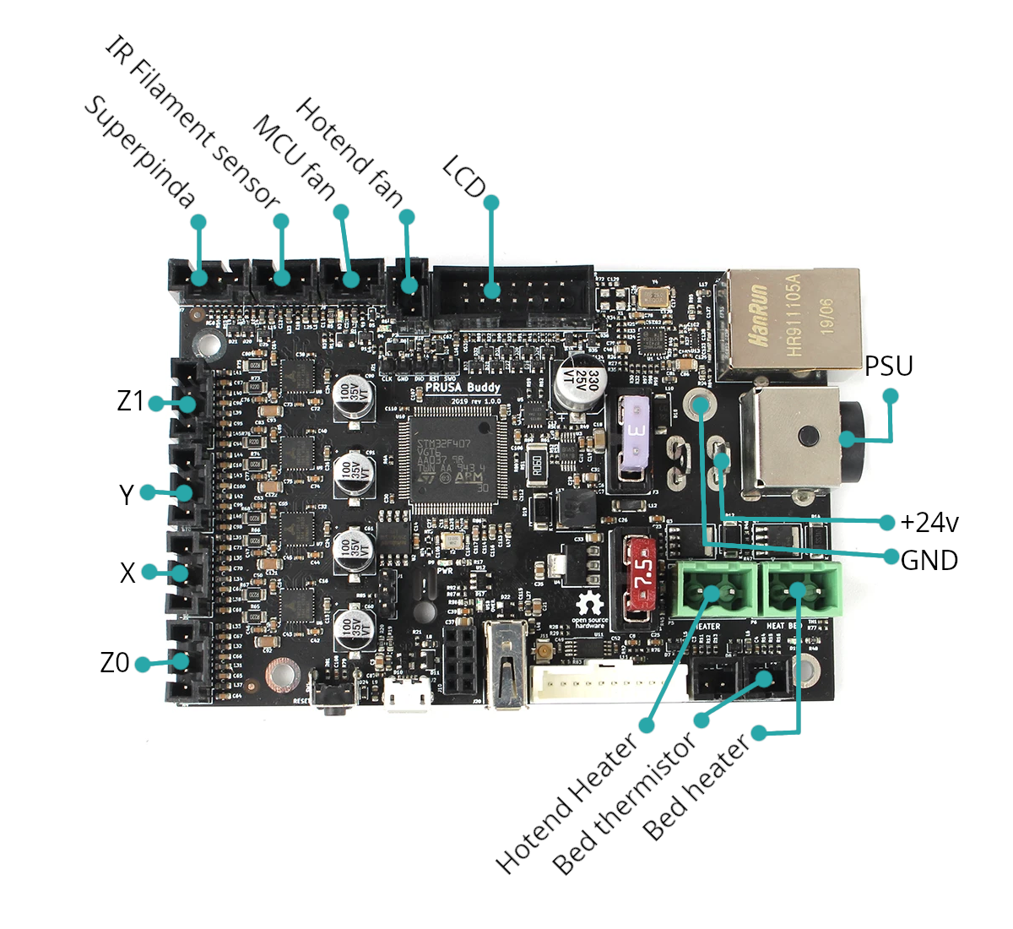
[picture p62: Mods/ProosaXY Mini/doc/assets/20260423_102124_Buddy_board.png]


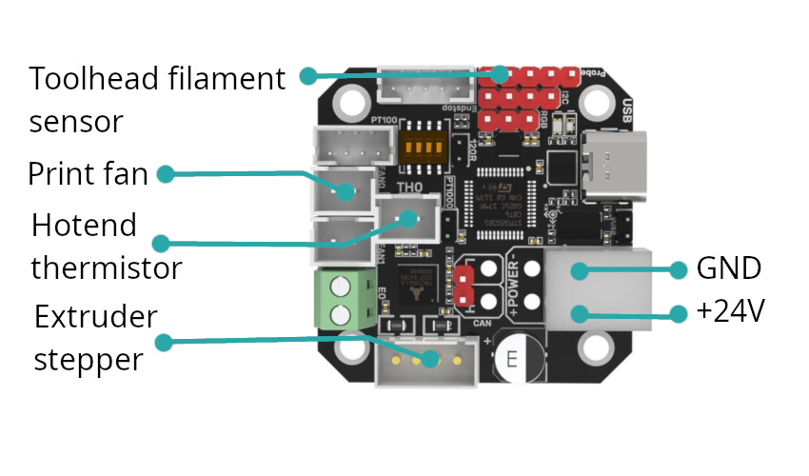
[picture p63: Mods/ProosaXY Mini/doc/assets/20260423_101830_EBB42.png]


## PSU wiring example

This is the ProosaXY Mini #SP00F

* IEC socket with master switch
* Standard IEC PSU cable wired to the MINI PSU inlet
* AC wires to the LRS-25-5 PSU
* +24v/GND from buddy board to EBB42 MCU
* +24v connection of buddy board are jumped

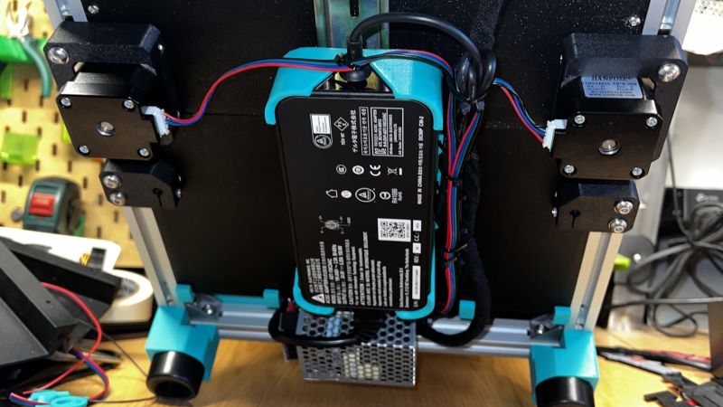
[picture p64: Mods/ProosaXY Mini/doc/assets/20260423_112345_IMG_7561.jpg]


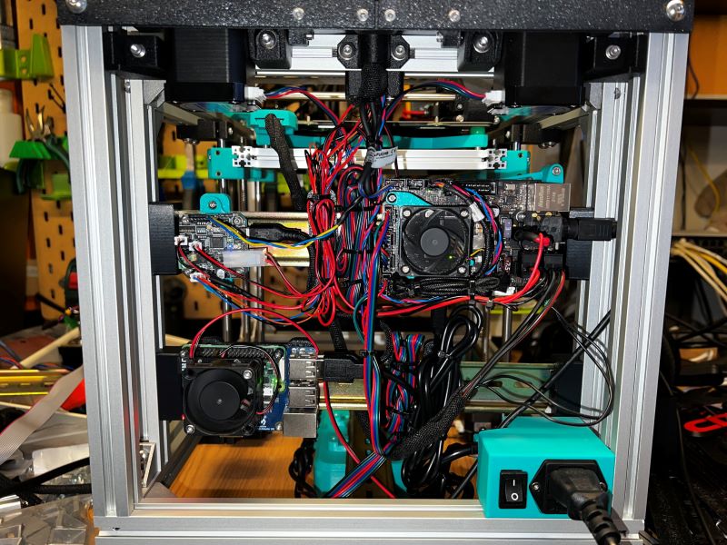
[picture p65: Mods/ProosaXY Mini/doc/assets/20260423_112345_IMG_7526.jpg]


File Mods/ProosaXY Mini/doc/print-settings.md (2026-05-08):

# ProosaXY MINI considerations

This is a small documentation page to guide you about some concerns.

## 1. Slicer settings

This is the setings I'm using actually.

* 0.2mm layer height
* Wall count: 5
* Top/bottom layer: 5
* Infill: 30%, with any gyroid variant

## 2. Filament

It depends on what you're looking for, PETG can withstand if you are not pushing the limits and you are only printing PLA, but honestly I recommended to print all parts with high temperature resistant filament.

If you want to reuse the stock motor steppers (that it's not recommended) you need at least ABS+GF or PC+ABS for motor mounts, stock steppers can do 10-15K accels with 200-250mm/s with 0.6-0.65amps but running very hot. (+80ºC)

Check the shrinkage of the filament !

## 3. Remove supports

Certain pieces like the LCD holder needs to remove the printable support.

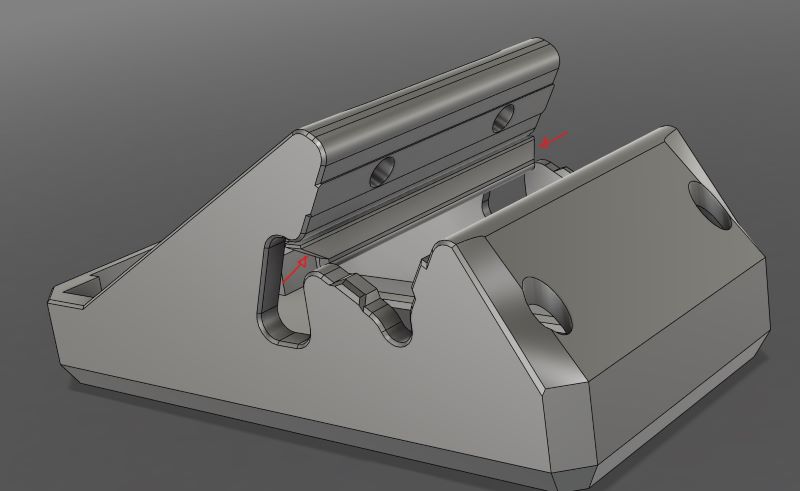
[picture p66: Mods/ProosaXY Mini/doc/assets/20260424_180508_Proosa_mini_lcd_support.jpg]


## 4. Parts required

The ProosaXY MINI uses a mix of standard ProosaXY parts and specific MINI parts.

| Group | From | Part | Quanty | Notes |
| :--- | --- | --- | --- | --- |
| XY Axis | ProosaXY | motor-support-body-left | 1 | |
| XY Axis | ProosaXY | motor-suport-body-right | 1 | |
| XY Axis | ProosaXY | motor-support-slider-left | 1 | |
| XY Axis | ProosaXY | motor-support-slider-right | 1 | |
| XY Axis | ProosaXY | left-motor-mount-base | 1 | This part will be hot |
| XY Axis | ProosaXY | left-motor-mount-cap | 1 | |
| XY Axis | ProosaXY | left-motor-mount-spacer | 1 | This part will be hot |
| XY Axis | ProosaXY | right-motor-mount-base | 1 | This part will be hot |
| XY Axis | ProosaXY | right-motor-mount-cap | 1 | |
| XY Axis | ProosaXY | right-motor-mount-spacer | 1 | This part will be hot |
| XY Axis | ProosaXY | motor-shaft-spacer | 1 | |
| XY Axis | MINI | y-carrier-cap-LM10**L**UU | 2 | Take care, LM10LUU for long bearing. |
| XY Axis | MINI | y-carrier-LM10**L**UU | 2 | Take care, LM10LUU for long bearing. |
| XY Axis | MINI | y-rod-cap-10mm | 4 | |
| XY Axis | ProosaXY | long-spacer | 2 | |
| XY Axis | ProosaXY | short-spacer | 8 | |
| XY Axis | MINI | rod-mount-10mm | 4 | |
| Z Axis  | ProosaXY | z-rod-bottom-mount-right | 2 | |
| Z Axis  | ProosaXY | z-rod-top-mount-right | 2 | |
| Z Axis  | ProosaXY | z-rod-bottom-mount-left | 2 | |
| Z Axis  | ProosaXY | z-rod-top-mount-left | 2 | |
| Z Axis  | MINI | bed-cable-cover-top | 1 | |
| Z Axis  | MINI | bed-cable-cover-bottom | 1 | |
| Z Axis  | MINI | extrusion-end-logo | 1 | MMU version available |
| Z Axis  | ProosaXY | Z-motor-mounter | 2 | |
| Z Axis  | ProosaXY | bed-LM8UU-mounter | 4 | |
| Z Axis  | ProosaXY | pom-nut-mounter | 2 | |
| Z axis  | MINI | prusa-mini-bed-helper | 1 | You can fit without.... but I do not recommend. This part will be hot |
| Panels  | MINI | back-panel-bottom-left | 1 | |
| Panels  | MINI | back-panel-bottom-right | 1 | |
| Panels  | MINI | back-panel-top-left | 1 | |
| Panels  | MINI | back-panel-top-right | 1 | |
| Panels  | MINI | back-panel-connector | 1 | MMU version available |
| Panels  | MINI | bottom-panel-back-left | 1 | |
| Panels  | MINI | bottom-panel-back-right | 1 | |
| Panels  | MINI | bottom-panel-front-left | 1 | |
| Panels  | MINI | bottom-panel-front-right | 1 | |
| Panels  | ProosaXY | bottom-panel-connector | 1 | |
| Panels  | ProosaXY | bottom-panel-clip | 6 | |
| Panels  | ProosaXY | y-cover-cap-mirror | 2 | Optional, but 100% recommended |
| Panels  | ProosaXY | y-cover-cap | 2 | Optional, but 100% recommended |
| Panels  | MINI | y-cover-body | 4 | Optional, but 100% recommended |
| Panels  | ProosaXY | panel-clip-housing | 12 | Only if you will put side panels |
| Panels  | ProosaXY | panel-clip-inner | 12 | Only if you will put side panelsOptiona |
| Panels  | ProosaXY | proosaxy-mini-big-logo | 1 | MMU version available |
| Panels  | MINI | cable-panel-back-cover | 1 | |
| Panels  | MINI | cable-panel-back-cover-mirror | 1 | |
| Panels  | MINI | cable-panel-bottom-cover | 1 | |
| Panels  | ProosaXY | bottom-back-panel-connector | 4 | |
| Others  | ProosaXY | foot-mounter-mX | 4 | Pick your version |

Toolhead section it depends of what do you want to fit, the following parts are intended to be paired with TZ-V6 2.0 hotend with V6 style nozzle. (V6 nozzle are 2mm taller of TZ nozzles) and magneto filament cutter from VzBot. We will not support the Prusa Mini hotend due their poor performance and tied to heatcreep due the ausence of real heatbreak.

The toolhead it's the same of the ProosaXY, if you don't want TZ-V6 select wathever you want :)

If you don't want the filament cutter, just drill the PTFE hole with 4mm bit and fit longer PTFE tube.

| Group | From | Part | Quanty | Notes |
| --- | --- | --- | --- | --- |
| Toolhead | ProosaXY | cable-end-mounter | 1 | |
| Toolhead | ProosaXY | strain-relief-end-mounter | 1 | |
| Toolhead | ProosaXY | Duct v2.1 straight low | 1 | This part will be very hot |
| Toolhead | ProosaXY/MMU | Extruder mount - Sherpa | 1 | Stronger version that standard, This part will be very hot |
| Toolhead | ProosaXY/MMU | Hotend mount - TZ-V6 | 1 | This part will be very hot, drill with 4mm bit if you don't want to use the filament cutter |
| Toolhead | <a href="https://github.com/Annex-Engineering/Annex-Engineering_User_Mods/tree/main/Extruders/Sherpa_Mini/Extruder_Mods/Gryp2-Housing_Core_with_filament_sensor">Annex user mod</a> | sherpa-core-with-d2f | 1 | Sherpa mini core with D2F sensor, This part will be very hot |
| Toolhead | ProosaXY/MMU | sherpa-idler-arm-strong | 1 | Stronger idler arm for fine sensor activation, This part will be very hot |
| Toolhead | ProosaXY | c_front_body | 1 | This part will be very hot |
| Toolhead | ProosaXY | c_back_body | 1 | This part will be very hot |
| Toolhead | ProosaXY | back-fan-mounter | 1 | This part will be very hot |
| Toolhead | ProosaXY | bottom-bearing-cap | 1 | critical part, This part will be very hot |
| Toolhead | ProosaXY | carrier-body | 1 | critical part, This part will be very hot |
| Toolhead | ProosaXY | duct-spacer | 1 | This part will be very hot |
| Toolhead | ProosaXY | hotend-bottom-mount | 1 | This part will be very hot |
| Toolhead | ProosaXY | probe-mounter | 1 | This part will be very hot |
| Toolhead | ProosaXY | top-bearing-cap | 1 | critical part, This part will be very hot |
| Toolhead | ProosaXY | belt-holder | 2 | Critical part, This part will be very hot |
| Toolhead | ProosaXY | belt-tensioner-cap | 2 | This part will be very hot |
| Toolhead | ProosaXY | back-fan-spacer | 3 | This part will be very hot |

Electronics,  you will need to complete your print list depending the components you will fit.

| Group | From | Part | Quanty | Notes |
| --- | --- | --- | --- | --- |
| Electronics | MINI | Proosa-mini-lcd-holder | 1 | MMU version available |
| Electronics | MINI | proosa-mini-xxxmmm-PSU-holder | 1 | Pick your version, measure your PSU |
| Electronics | MINI | ebb42-din-mount | 1 | Only of you are using this MCU, uses 50mm spacing |
| Electronics | MINI | buddy-mcu-din-mount | 1 | Uses 50mm spacing |
| Electronics | MINI | buddy-mcu-fan-mount | 1 | |
| Electronics | MINI | buddy-mcu-clip | 1 | |
| Electronics | MINI | low-profile-din-clip | 6 | 50mm spacing |
| Electronics | ProosaXY | Raspberry pi mounts | 1 | |
| Electronics | ProosaXY | LRS-25-5 PSU mounts | 1 | |
| Electronics | ProosaXY | bottom-din-holder | 2 | |
| Electronics | ProosaXY | back-din-holder | 4 | |
| Electronics | ProosaXY | optional_din-ziptie | n | |

Tools and jigs

| Group | From | Part | Quanty | Notes |
| :--- | --- | --- | --- | --- |
| Tools | ProosaXY | 2020 drill jig | 1 | Only if you need drill the extrusions |
| Tools | ProosaXY | 2020 holder | 1 | Only if you need drill the extrusions |
| Tools | ProosaXY | 45mm mark jig | 1 | Only if you need drill the extrusions |
| Tools | ProosaXY | mr115 holder drill guide  | 1 | Only if you need drill the extrusions |
| Tools | ProosaXY | bearing-stack-holder-tool | 1 | Needed to fit the F623 bearing stacks |
| Tools | ProosaXY | belt-position-jig | 1 | Helper to situate the same distance on each side to tune the belts |
| Tools | MINI | z-rod-mount-aligner | 1 | You can use instead a caliper and measure 48mm from the extrusion. |
| Tools | MINI | silicon-mod-jig | 1 | |

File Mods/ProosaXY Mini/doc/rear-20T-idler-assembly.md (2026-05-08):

# ProosaXY MINI rear 20T idlers

To avoid a complete redesign of motor mounts we decided to made this adaptation to able to use 20T idlers with 4MM ID, that are the best because the 4MM ID ones have the bigger bearing.

We need a to put a 8.5x3x4 spacer, if you cant source one you can fabricate using a 3mm ID / 4mm OD steel tube and cut to correct lenght.

<p style="text-align:center;">
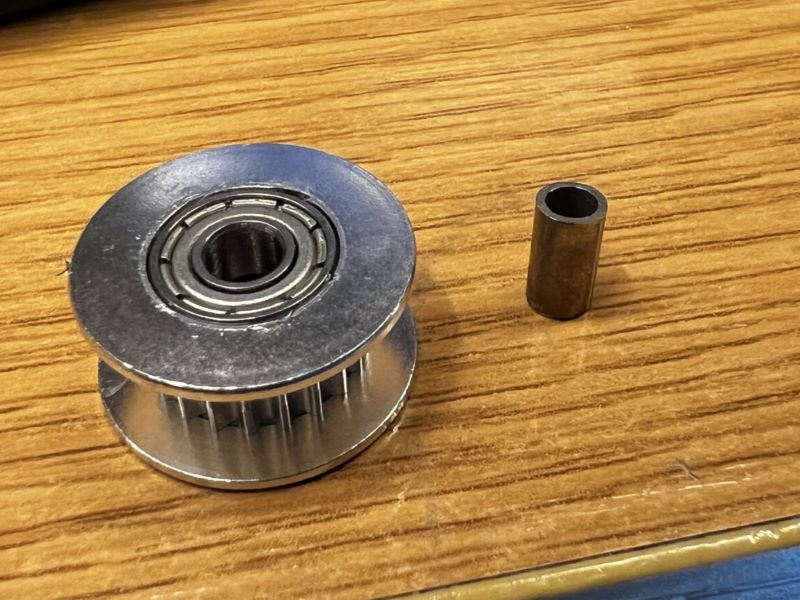
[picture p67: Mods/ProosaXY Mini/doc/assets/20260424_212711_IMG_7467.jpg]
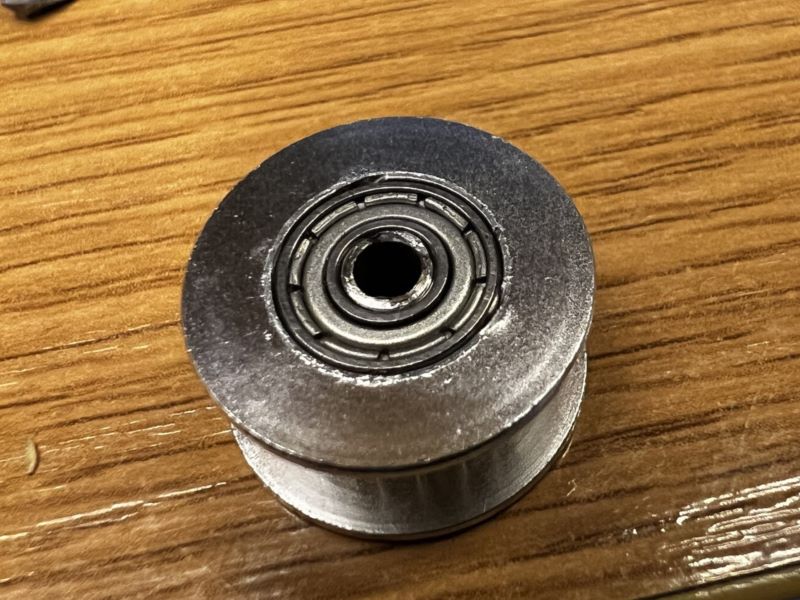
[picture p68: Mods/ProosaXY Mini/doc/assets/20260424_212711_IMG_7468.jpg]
 
</p>

There is no tradeoffs on this adaptation, the bearing stays in place without any play.

<p style="text-align:center;">
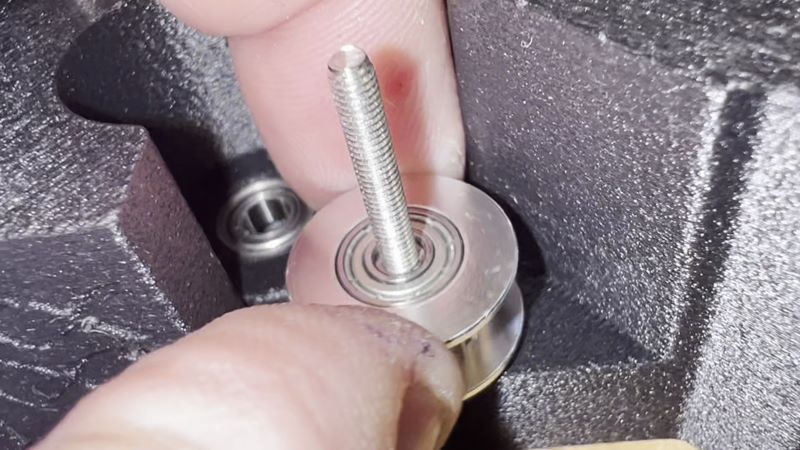
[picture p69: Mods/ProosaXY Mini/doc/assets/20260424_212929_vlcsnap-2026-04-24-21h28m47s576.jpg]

</p>

The y-carrier ones are assembled with 4mm screw, no adaptatio needed on this ones.

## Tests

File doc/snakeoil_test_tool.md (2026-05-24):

# Snakeoil Test tool

We developed a test tool to ensure a correct printing of the printed parts.

Some parts require to insert a bearing, a smooth rod, etc...

It's under STLs/tools/

Today we have a very well tuned profiles by the manufacturers, but most of them do not tune the shrinkage ratio, this is very important, even PLA Shrink.

You need to have a proper flow calibration and pressure advance.

You have a very good manuals here from Ellis. [PA Calibration](https://ellis3dp.com/Print-Tuning-Guide/articles/pressure_linear_advance/tower_method.html) and [Flow calibration](https://ellis3dp.com/Print-Tuning-Guide/articles/extrusion_multiplier.html)

With this test you will calibrate the shrink ratio

Just print with your normal profile, using 3-4 perimeters, this is important due we need to test if your profile overheat and do poor overhangs.

Leave cool at least 20 minutes and measure the printed piece, you will notice the printer part will not meet the 100mm lenght

Don't worry about that, this is the expected without the shrink ratio configured.

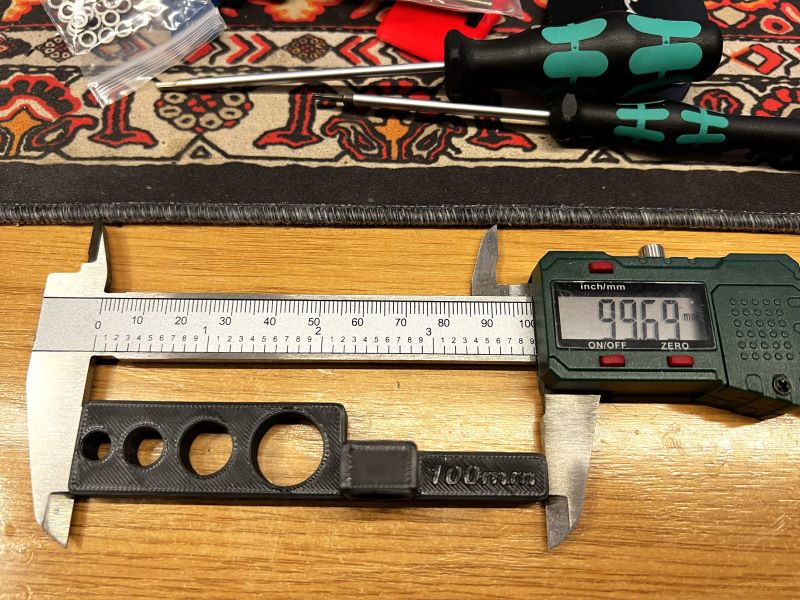
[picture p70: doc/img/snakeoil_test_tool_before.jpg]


Now we pick these values and we are going to fill the shrink ratio / shrink compensation under filament configuration of our slicer.

With my example you will input 99.69% on shrinkage.

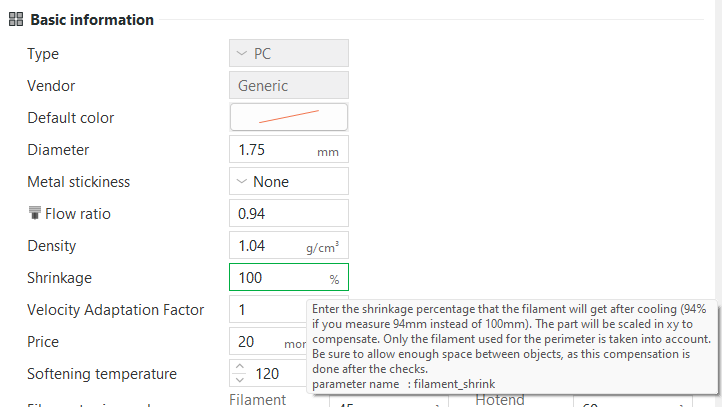
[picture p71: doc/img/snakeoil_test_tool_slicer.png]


Reprint the part.

Now the expected is the printed part will meet the 100mm+-0.01mm

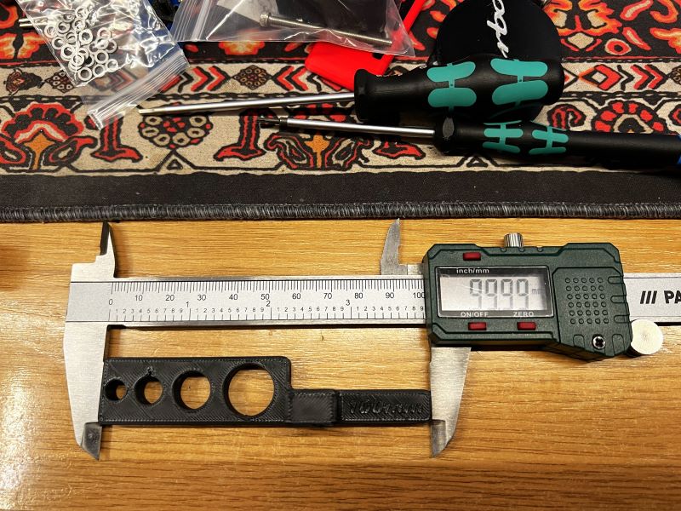
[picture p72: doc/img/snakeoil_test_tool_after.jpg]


From left to right the holes are intended to test.

* Bed spacer (helper), very hard to push into, is expected, to avoid to fall off
* 8mm smooth rod
* MR115 Bearing
* LM8UU Bearing
* MR115 Bearing (vertical one)
* M5 screw (vertical one)

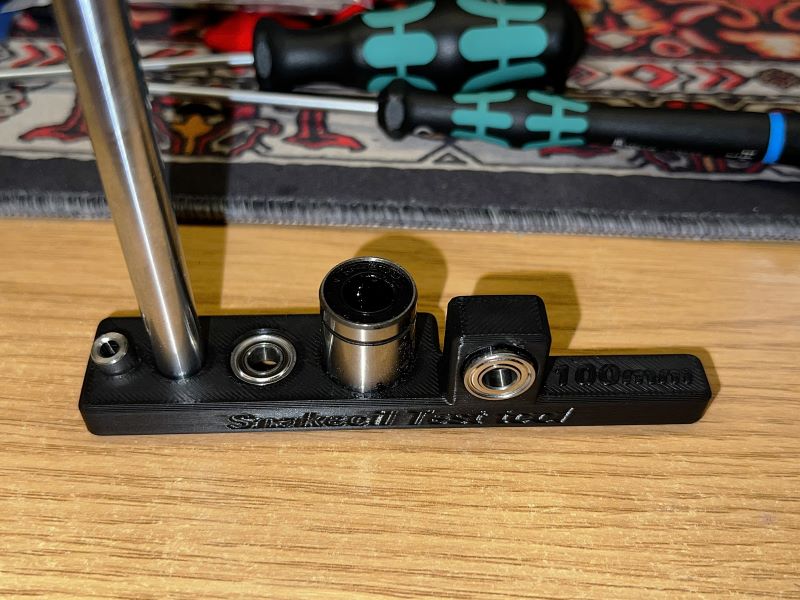
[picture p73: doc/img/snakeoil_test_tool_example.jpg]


Some videos.

[Snakeoil test tool demostration video](https://www.youtube.com/watch?v=dke0h-PXOAI)
[ProosaXY Mini printing snakeoil test tool](https://www.youtube.com/watch?v=qTiXc0uOBks)

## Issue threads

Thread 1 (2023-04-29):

Another approach

espr14, 2023-04-29:
Hello. I was also trying to convert Prusa i3 MK3 to coreXY. Maybe you can be inspired by my approach and take some printed parts. The main difference is use of one extra ALU frame and no extra ALU profiles. The frame is much more rigid and has very low skew compared to bolted ALU profiles. Also the power supply holds the frame. Unfortunatelly, I haven't finished the Z axis.

https://www.printables.com/model/72811-prusa-i3-mk3-corexy-3d-printer

espr14, 2023-04-29:
If you'll be modding Prusa MINI I can help.

ChipCE, 2023-04-30:
Hi, that look nice!
About the mini, I'm not sure if the cost is still in resonable range. Build the tic-tac from scratch might be a better option.
https://www.printables.com/model/164038-tic-tac-miniaturised-v-minion

About the fw, what fw are you familiar with?

espr14, 2023-04-30:
I thought about MINI in the box with double Z. This would be cheaper than Voron 0.2, still.

I'm maintainer of Snake FW (previously Llama FW) based on Buddy FW for MINI, MK4 and XL. I did some changes in MK3 FW but I don't have the printer any more.
https://github.com/Snake-FW/P32-FW

ChipCE, 2023-05-01:
> I thought about MINI in the box with double Z. This would be cheaper than Voron 0.2, still.

i did this back then with a scaled down bear frame and custom bowden bear-extruder. It can run at 250% speed of the mk3 without a sweat.

https://photos.app.goo.gl/DhzNpycHasufgsmX9

> I'm maintainer of Snake FW (previously Llama FW) based on Buddy FW for MINI, MK4 and XL. I did some changes in MK3 FW but I don't have the printer any more.

Great, I would love to have you join the team and help us with Marlin fw.
I made the TH3D online compiler few years ago, but have to re-flash firmware each change is far over my patience.

espr14, 2023-05-01:
Nice. But I'd like enclosed printer more than the max. speed. I don't like the X axis motor being out of the box in the i3 printers. In my custom 3D printer I've put X motor between the Y rods like in Chaos MK3 Box (https://www.printables.com/model/103675-prusa-box-mk3s-chaos-edition-chaosbox/collections).

I can help with the FW. But I don't have the Prusa i3 MK3 board you're using.

Closed 2024-04-24.

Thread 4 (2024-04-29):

Some Questions

3DCoded, 2024-04-29:
I am looking into building this for my Prusa MK3S+, but I have a few questions first:
This is (will be) a custom-built Prusa MK3S+ made from the frame left over after I did the Bear Upgrade. My only significant changes were using 0.9º steppers on x and y (high torque on y) and making a custom dual extruder head.

- What parts need to be removed/modified from the original Prusa to do this upgrade (so I don't buy them)?
- Where do you buy your aluminum extrusions and DIN rails (I couldn't find the right lengths on Amazon or Alieexpress)?
- What's the status of the build instructions? I don't think I'll be able to build this without them, as this will be my first time messing with CoreXY.

ChipCE, 2024-05-03:
> I am looking into building this for my Prusa MK3S+, but I have a few questions first: This is a custom-built Prusa MK3S+ made from the frame left over after I did the Bear Upgrade. My only significant changes were using 0.9º steppers on x and y (high torque on y) and making a custom dual extruder head.
>
I have the same 0.9º  E3D high torque motor on mine too. They are work great up to about 300mm/s.
>     * What parts need to be removed/modified from the original Prusa to do this upgrade (so I don't buy them)?
>
The list available on our [google doc BOM list](https://docs.google.com/spreadsheets/d/1j1bnA8rNjDqpTVEdiqrsRlNeggI6PYRAoSBm1F8bvCs/edit)

>     * Where do you buy your aluminum extrusions and DIN rails (I couldn't find the right lengths on Amazon or Alieexpress)?
>

Bought mine from Misumi. You can get our open-beta kit from [Fabreeko](https://www.fabreeko.com/products/proosa-xy-conversion-for-mk3s-to-core-xy-by-snakeoilxy-open-beta). It have most of the parts you will need.

>     * What's the status of the build instructions? I don't think I'll be able to build this without them, as this will be my first time messing with CoreXY.
We only have a simple build log, and some live build videos on our [youtube channel](https://www.youtube.com/channel/UCIwlxzAJvDTgEfAodtsRMdw) now.

If you want faster response, please visit our discord server.

Closed 2024-05-13.

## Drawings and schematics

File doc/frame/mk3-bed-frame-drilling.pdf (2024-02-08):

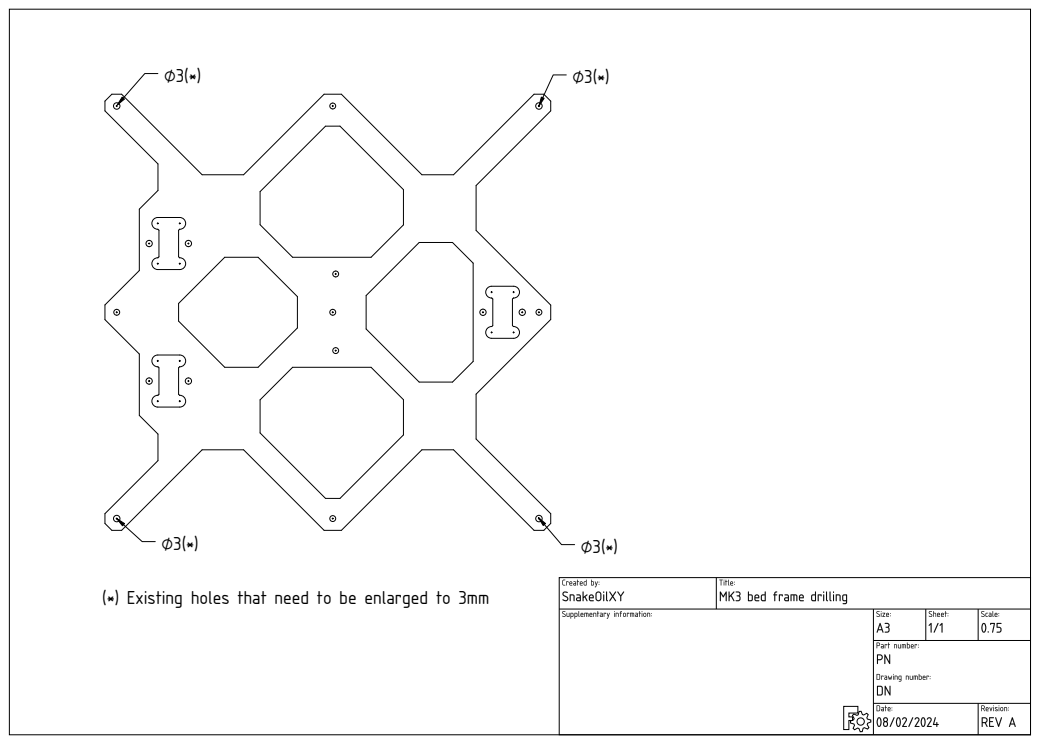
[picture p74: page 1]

(*) Existing holes that need to be enlarged to 3mm

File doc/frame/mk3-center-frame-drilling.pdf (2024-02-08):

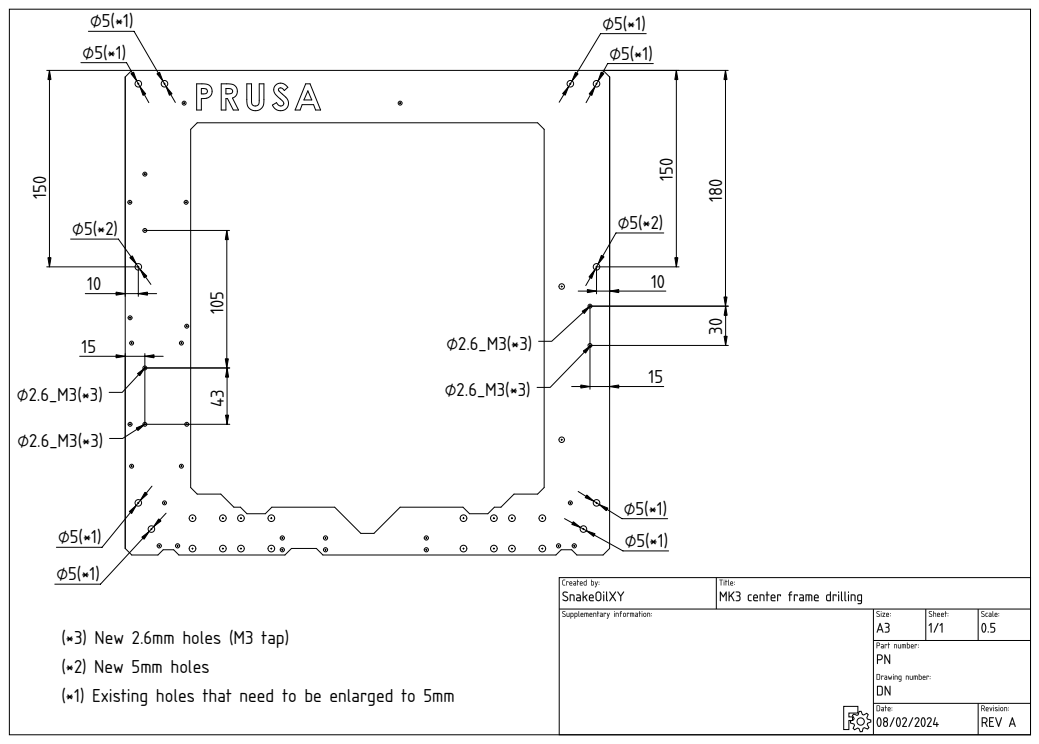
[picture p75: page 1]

(*3) New 2.6mm holes (M3 tap)
(*2) New 5mm holes
(*1) Existing holes that need to be enlarged to 5mm

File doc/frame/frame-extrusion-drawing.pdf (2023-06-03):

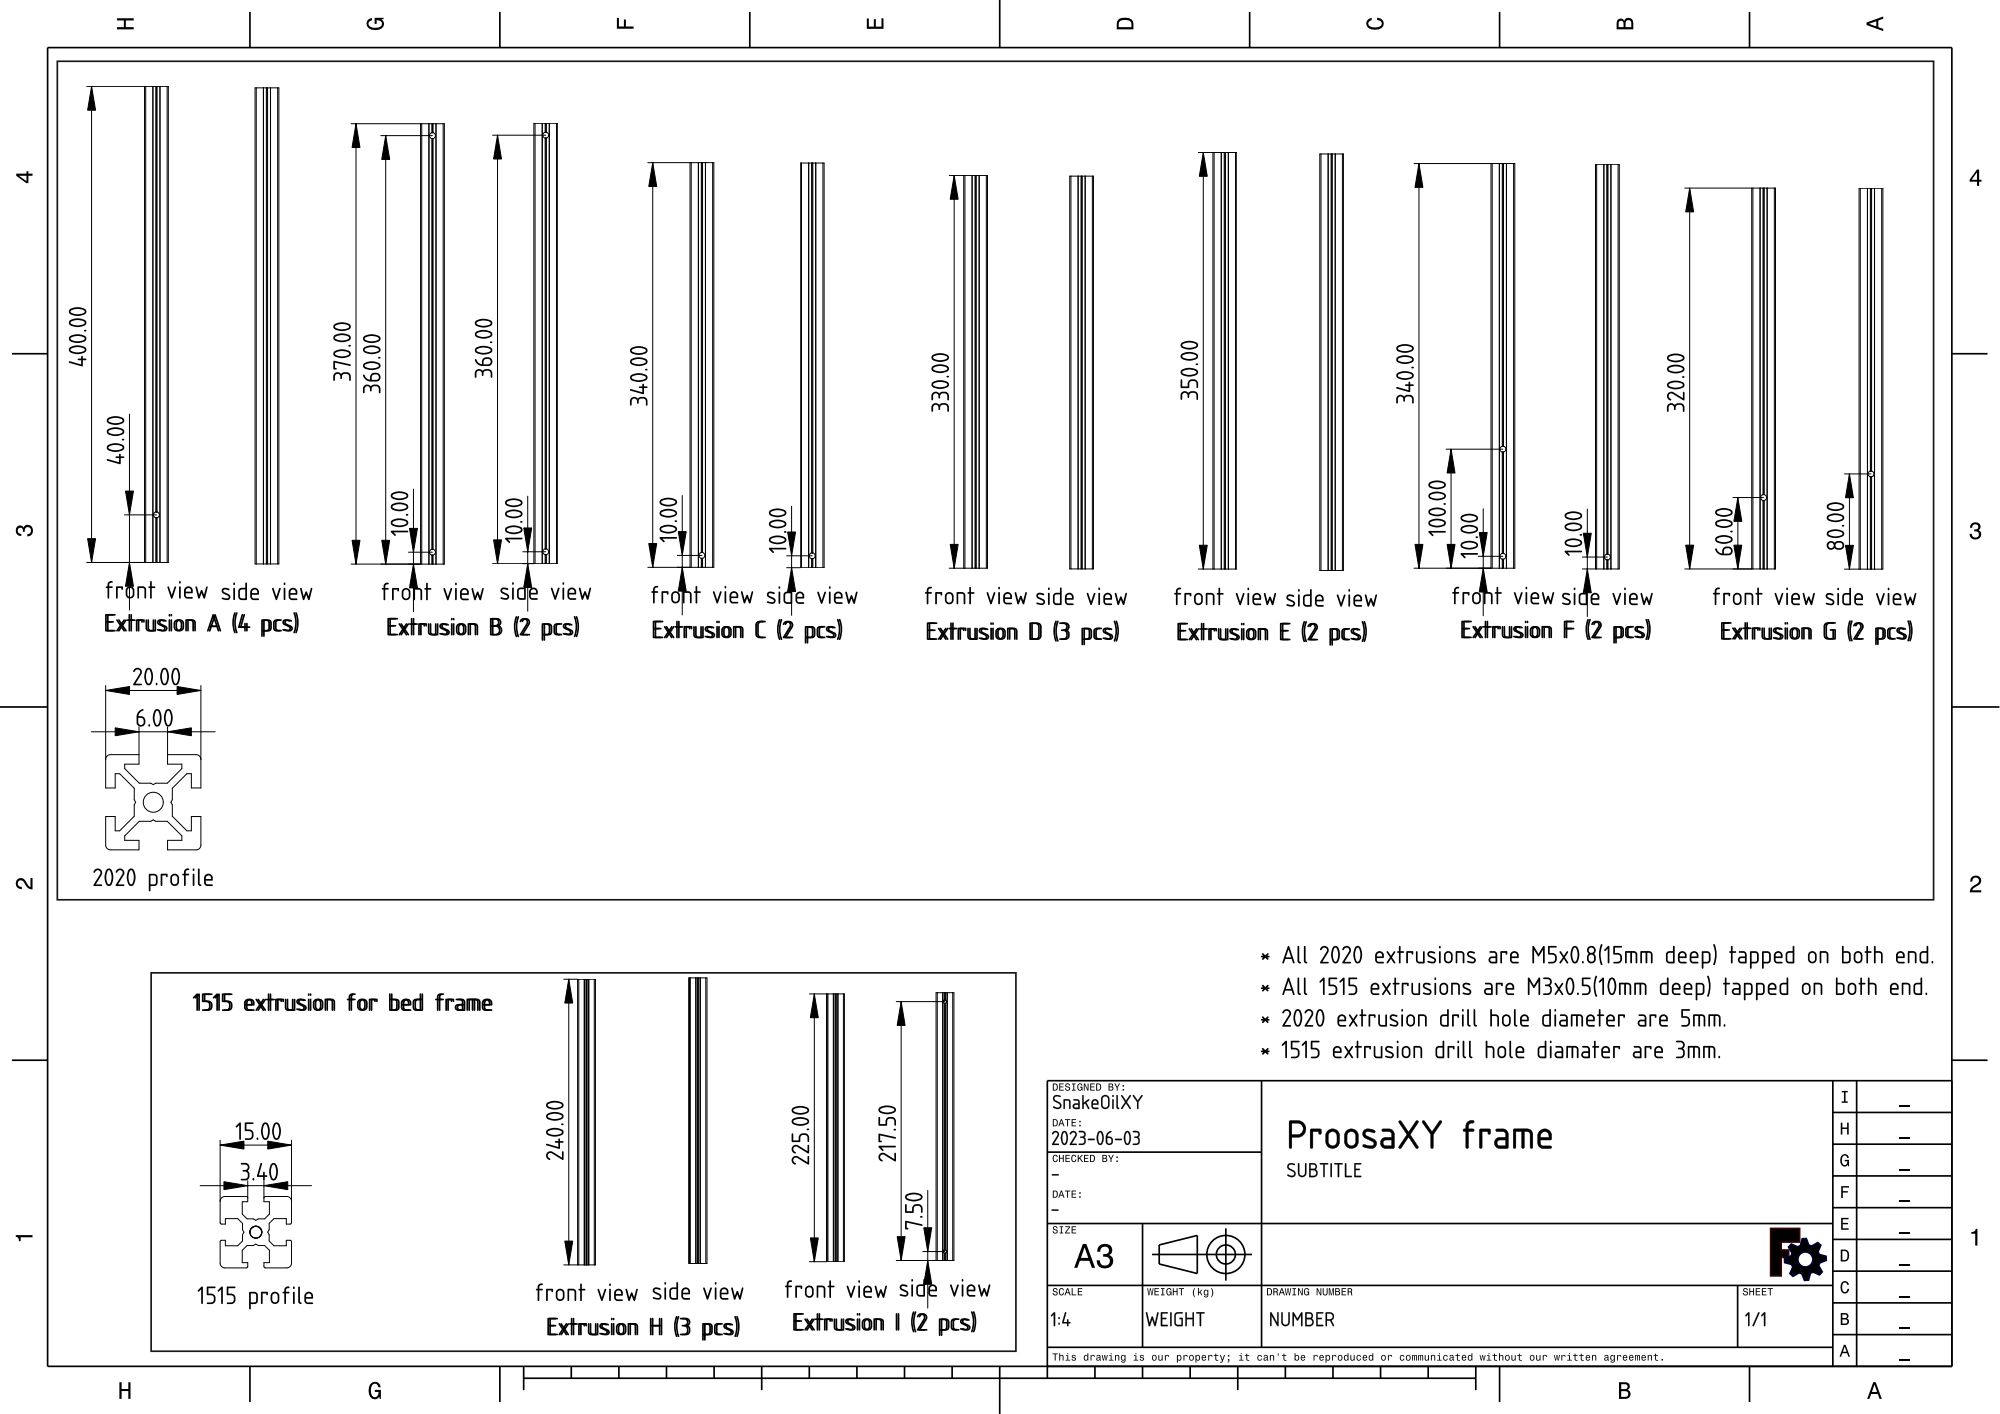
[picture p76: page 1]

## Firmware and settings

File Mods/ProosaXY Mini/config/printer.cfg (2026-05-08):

#  ____                           __  ____   __  __  __ ___ _   _ ___ 
# |  _ \ _ __ ___   ___  ___  __ _\ \/ /\ \ / / |  \/  |_ _| \ | |_ _|
# | |_) | '__/ _ \ / _ \/ __|/ _` |\  /  \ V /  | |\/| || ||  \| || | 
# |  __/| | | (_) | (_) \__ \ (_| |/  \   | |   | |  | || || |\  || | 
# |_|   |_|  \___/ \___/|___/\__,_/_/\_\  |_|   |_|  |_|___|_| \_|___|

# This config is intended to be used with Prusa buddy board and BTT EBB42, if you want to
# use different MCU you need to check the pins

# This config is intended to be paired with tradrack config to have working filament sensor
# If you want standard IR filament sensor just plug the IR sensor on buddy board and uncoment
# the filament section of this config.

# Do not use adaptive mesh or KAMP plugins. The standard 3x3 bed mesh is fast enough and avoid
# the magnet field of the underbed magnets, leave the bed_mesh section unchanged if you don't
# know what are you doing

# This config uses TR8X8 leadscrew motors for Z, because for me it's cheaper than buy other
# TR8x4, I have a bunch of old MK3s Z motors.

# This config uses OMC HE19 2A steppers to max out the printer capabilities, it's a cheap upgrade
# 20€/25$ for a pair of good steppers or less.

#                  __ _ _       _     _          _               _    
#  _ __  _ __ ___ / _| (_) __ _| |__ | |_    ___| |__   ___  ___| | __
# | '_ \| '__/ _ \ |_| | |/ _` | '_ \| __|  / __| '_ \ / _ \/ __| |/ /
# | |_) | | |  __/  _| | | (_| | | | | |_  | (__| | | |  __/ (__|   < 
# | .__/|_|  \___|_| |_|_|\__, |_| |_|\__|  \___|_| |_|\___|\___|_|\_\
# |_|                     |___/                                       

# Replace the IDs of the MCU's with yours on MCU section

# 1- This config comes with input shaper activated, with the values of standard proosaXY, works
# 2- with ProosaXY mini well but need to be tuned with real values.
# 3- Ensure the buddy fan is working to avoid overheating, it's critical, low temps when on,
# high temps if not.
# 4- If you are using TR8x4 leadscrew change this on Stepper section put rotation_distance: 4
# 5- If you are using OEM 1A high inductance steppers change this on Stepper section
# 5- Redo the PID for the extruder heater.
# 6- Do not forget to put your print_start/print_end macro ;)

[include mainsail.cfg]
[pause_resume]
[exclude_object]

[idle_timeout]
timeout: 1200
    
#[include config/plugins/tradrack/*.cfg]

[virtual_sdcard]
path: ~/printer_data/gcodes

#  __  __  ____ _   _ 
# |  \/  |/ ___| | | |
# | |\/| | |   | | | |
# | |  | | |___| |_| |
# |_|  |_|\____|\___/ 

[mcu]
serial: /dev/serial/by-id/usb-Klipper_stm32f407xx_56003A001150315239353820-if00

[mcu ebb]
serial: /dev/serial/by-id/usb-Klipper_stm32g0b1xx_410012000250505539323520-if00

[display]
lcd_type: st7789v
spi_bus: spi2a
rst_pin: PC8
cs_pin: PC9
rs_pin: PD11
encoder_pins: ^PE13, ^PE15
click_pin: ^!PE12
display_group: _default_20x4

[temperature_sensor buddy_board]
sensor_type: temperature_mcu
sensor_mcu: mcu
min_temp: 10
max_temp: 100

[temperature_sensor ebb]
sensor_type: temperature_mcu
sensor_mcu: ebb
min_temp: 10
max_temp: 100

[temperature_sensor raspberry_pi]
sensor_type: temperature_host
min_temp: 10
max_temp: 100

#  ____       _       _            
# |  _ \ _ __(_)_ __ | |_ ___ _ __ 
# | |_) | '__| | '_ \| __/ _ \ '__|
# |  __/| |  | | | | | ||  __/ |   
# |_|   |_|  |_|_| |_|\__\___|_|   

# Standard ProosaXY IS
[input_shaper]
shaper_freq_x: 58.2
shaper_type_x: mzv
shaper_freq_y: 42.8
shaper_type_y: mzv

[printer]
kinematics: corexy
max_velocity: 500
max_accel: 20000
#max_accel_to_decel: 15000
max_z_velocity: 25
max_z_accel: 1000
square_corner_velocity: 25

#  ____  _                             
# / ___|| |_ ___ _ __  _ __   ___ _ __ 
# \___ \| __/ _ \ '_ \| '_ \ / _ \ '__|
#  ___) | ||  __/ |_) | |_) |  __/ |   
# |____/ \__\___| .__/| .__/ \___|_|   
#               |_|   |_|              

[stepper_x]
step_pin: PD1
dir_pin: PD0
enable_pin: !PD3
microsteps: 32 # Better quality, less noise
# microsteps: 16 # You may need if want to use OEM high inductance stepperrs
rotation_distance: 40
full_steps_per_rotation:200
endstop_pin: tmc2209_stepper_x:virtual_endstop
position_endstop: -2
position_max: 193.5
position_min : -3
homing_speed: 40
homing_retract_dist: 0

[tmc2209 stepper_x]
uart_pin: PD5
uart_address: 1
run_current: 1.000 # OMC HE19 2A Stepper
# run_current: 0.600 # OEM high inductance steppers
sense_resistor: 0.22
interpolate: false
stealthchop_threshold: 0
diag_pin: ^PE2
driver_SGTHRS: 100

[stepper_y]
step_pin: PD13
dir_pin: PD12
enable_pin: !PD14
microsteps: 32 # Better quality, less noise
# microsteps: 16 # You may need if want to use OEM high inductance stepperrs
rotation_distance: 40
full_steps_per_rotation:200
endstop_pin: tmc2209_stepper_y:virtual_endstop
position_endstop: -5
position_max: 190
position_min : -5
homing_speed: 40
homing_retract_dist: 0

[tmc2209 stepper_y]
uart_pin: PD5
uart_address: 3
run_current: 1.000 # OMC HE19 2A Stepper
# run_current: 0.600 # OEM high inductance steppers
sense_resistor: 0.22
interpolate: false
stealthchop_threshold: 0
diag_pin: ^PE1
driver_SGTHRS: 100

[stepper_z]
step_pin: PD4
dir_pin: !PD15
enable_pin: !PD2
microsteps: 32
rotation_distance: 8 # TR8x8 leadscrew
#rotation_distance: 4 # TR8x4 leadscrew
full_steps_per_rotation:200 
position_max: 210
position_min : -5
homing_speed: 10
endstop_pin: probe:z_virtual_endstop

[tmc2209 stepper_z]
uart_pin: PD5
uart_address: 0
run_current: 0.35
sense_resistor: 0.22
interpolate: false
stealthchop_threshold: 99999

[stepper_z1]
step_pin: PD9
dir_pin: !PD8
enable_pin: !PD10
microsteps: 32
rotation_distance: 8 # TR8x8 leadscrew
#rotation_distance: 4 # TR8x4 leadscrew
full_steps_per_rotation:200

[tmc2209 stepper_z1]
uart_pin: PD5
uart_address: 2
run_current: 0.35
sense_resistor: 0.22
interpolate: false
stealthchop_threshold: 99999

#  _____      _                  _           
# | ____|_  _| |_ _ __ _   _  __| | ___ _ __ 
# |  _| \ \/ / __| '__| | | |/ _` |/ _ \ '__|
# | |___ >  <| |_| |  | |_| | (_| |  __/ |   
# |_____/_/\_\\__|_|   \__,_|\__,_|\___|_|   
#  ( _ )   | |__   ___  __| |                
#  / _ \/\ | '_ \ / _ \/ _` |                
# | (_>  < | |_) |  __/ (_| |                
#  \___/\/ |_.__/ \___|\__,_|    

[extruder]
step_pin: ebb:PD0
dir_pin: !ebb:PD1
enable_pin: !ebb:PD2
# Sherpa mini
rotation_distance: 22.67895
gear_ratio: 50:10
microsteps: 16
full_steps_per_rotation: 200
nozzle_diameter: 0.400
filament_diameter: 1.750
max_extrude_only_distance: 250
max_extrude_cross_section: 50
min_temp: -10
max_temp: 310
max_power: 1.0
min_extrude_temp: 150
#smooth_time: 2.0
heater_pin: PB1
sensor_pin:  ebb:PA3
sensor_type: ATC Semitec 104GT-2
#control: pid
#pid_Kp: 33.265
#pid_Ki: 14.784
#pid_Kd: 18.711

[tmc2209 extruder]
uart_pin: ebb:PA15
run_current: 0.750
hold_current: 0.150
sense_resistor: 0.110
interpolate: false
stealthchop_threshold: 0

[heater_bed]
heater_pin: PB0 # bed
sensor_pin: PA4 # TB
sensor_type: Generic 3950
control: pid
pid_Kp: 120
pid_Ki: 1.5
pid_Kd: 600
min_temp: 10
max_temp: 110

#  _                   _ _             
# | |    _____   _____| (_)_ __   __ _ 
# | |   / _ \ \ / / _ \ | | '_ \ / _` |
# | |__|  __/\ V /  __/ | | | | | (_| |
# |_____\___| \_/ \___|_|_|_| |_|\__, |
#                                |___/ 

[probe]
pin: PA8
x_offset: 28.5
y_offset: -4
#z_offset: 0.0
speed: 10 #7.5
samples: 2
sample_retract_dist: 0.5
samples_result: median
samples_tolerance: 0.050
samples_tolerance_retries: 2
#activate_gcode:
#deactivate_gcode:

[safe_z_home]
home_xy_position: 90,90
z_hop: 6

[z_tilt]
# the point of the motor (or leadscrew)
z_positions:
	220, 90
	-25, 90
points:
    140, 90
	1.5, 90
speed: 100
horizontal_move_z: 10
retries: 10
retry_tolerance: 0.015

[bed_mesh]
algorithm: bicubic
fade_end: 10
horizontal_move_z: 2
mesh_max: 160,150
mesh_min: 30, 30
#mesh_pps: 3
probe_count: 3,3
speed: 400
adaptive_margin: 5

#  _____               
# |  ___|_ _ _ __  ___ 
# | |_ / _` | '_ \/ __|
# |  _| (_| | | | \__ \
# |_|  \__,_|_| |_|___/

#	Hotend Fan
[heater_fan hotend_fan]
pin: PE9
max_power: 1.0
kick_start_time: 0.5
heater: extruder
heater_temp: 50.0
shutdown_speed: 1
tachometer_pin: PE14

# Print fan
[fan]
pin: ebb:PA0
kick_start_time: 0.5
off_below: 0.05

# Buddy board fan
[controller_fan controller_fan]
pin: PE11
kick_start_time: 0.5
heater: extruder
max_power: 1


#*# <---------------------- SAVE_CONFIG ---------------------->
#*# DO NOT EDIT THIS BLOCK OR BELOW. The contents are auto-generated.
#*#
#*# [bed_mesh default]
#*# version = 1
#*# points =
#*# 	0.054375, 0.041250, 0.083125
#*# 	0.003125, 0.031250, 0.035000
#*# 	0.068125, 0.038125, 0.055625
#*# x_count = 3
#*# y_count = 3
#*# mesh_x_pps = 2
#*# mesh_y_pps = 2
#*# algo = bicubic
#*# tension = 0.2
#*# min_x = 30.0
#*# max_x = 160.0
#*# min_y = 30.0
#*# max_y = 150.0
#*#
#*# [probe]
#*# z_offset = 0.975
#*#
#*# [extruder]
#*# control = pid
#*# pid_kp = 41.551
#*# pid_ki = 21.307
#*# pid_kd = 20.257

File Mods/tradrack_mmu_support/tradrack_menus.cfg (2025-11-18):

# Menus for tradrack
# Just include this cfg on printer.cfg or reference to it.

[menu __main __tradrack]
type: list
name: Tradrack
index: 2

[menu __main __tradrack __tr_home]
type: command
enable: {not printer.idle_timeout.state == "Printing"}
name: Home tradrack
gcode:
  TR_HOME

[menu __main __tradrack __tr_resume]
type: command
enable: {not printer.idle_timeout.state == "Printing"}
name: Resume
gcode:
  TR_RESUME

[menu __main __tradrack __tr_unload_toolhead]
type: command
enable: {not printer.idle_timeout.state == "Printing"}
name: Unload Toolhead
gcode:
  TR_UNLOAD_TOOLHEAD

[menu __main __tradrack __tr_servo_up]
type: command
enable: {not printer.idle_timeout.state == "Printing"}
name: Servo UP
gcode:
  TR_SERVO_UP

[menu __main __tradrack __tr_servo_down]
type: command
enable: {not printer.idle_timeout.state == "Printing"}
name: Servo DOWN
gcode:
  TR_SERVO_DOWN

[menu __main __tradrack __tr_go_lane]
type: input
name: Go to Lane: {'%d' % menu.input}
enable: {not printer.idle_timeout.state == "Printing"}
input: {printer.save_variables.tr_active_lane | default(0)}
input_min: 0
input_max: {printer.configfile.config.trad_rack.lane_count}
input_step: 1
gcode:
  TR_GO_TO_LANE LANE={menu.input | int}

[menu __main __tradrack __tr_load_lane]
type: input
name: Load Lane: {'%.d' % menu.input}
enable: {not printer.idle_timeout.state == "Printing"}
input: 0
input_min: 0
input_max: {printer.configfile.config.trad_rack.lane_count}
input_step: 1
gcode:
  TR_LOAD_LANE LANE={menu.input | int}

[menu __main __tradrack __tr_load_toolhead]
type: input
name: Load Toolhead: {'%.d' % menu.input}
enable: {not printer.idle_timeout.state == "Printing"}
input: 0
input_min: 0
input_max: {printer.configfile.config.trad_rack.lane_count}
input_step: 1
gcode:
  TR_LOAD_TOOLHEAD LANE={menu.input | int}

[menu __main __tradrack __tr_active_lane]
type: input
name: Set active Lane: {'%.d' % menu.input}
enable: {not printer.idle_timeout.state == "Printing"}
input: 0
input_min: 0
input_max: {printer.configfile.config.trad_rack.lane_count}
input_step: 1
gcode:
  TR_SET_ACTIVE_LANE LANE={menu.input | int}

[menu __main __tradrack __discard_bowden]
type: command
name: Discard bowden lenght
gcode:
  TR_DISCARD_BOWDEN_LENGTHS

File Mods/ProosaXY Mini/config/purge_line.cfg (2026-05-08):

# Proosa Mini purge line
[gcode_macro PURGE_LINE]
gcode:
  G0 X0 Y-3 F10000                           # Go to starting point
  G0 Z0.4                                               # Raise Z to 0.4
  G91                                                   # Incremental positioning 
  G1 X100 E60  F900
  G1 X80 E40 F900                                     # Primeline
  G90                                                   # Absolute position

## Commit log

2023-04-10 add y carrier common
    [y-carrier-draf.FCStd, y-carrier.FCStd]
2023-04-11 add y carrier back plate
    [y-carrier.FCStd]
2023-04-13 add frame
    [frame-assembly.FCStd, x-carrier.FCStd]
2023-04-25 update BOM
    [x-carrier.FCStd, y-carrier.FCStd, y-rod-mount.FCStd]
2023-04-30 complete xy axis
    [1x_motor-mount-base-left.stl, 1x_motor-mount-base-right.stl, 1x_motor-mount-cap-left.stl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]
2023-05-07 update xy axis parts
    [1x_left-motor-mount-base.stl, 1x_left-motor-mount-cap.stl, 1x_left-motor-mount-spacer.stl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]
2023-05-08 update ab motor mount
    [1x_left-motor-mount-base.stl, 1x_left-motor-mount-cap.stl, 1x_right-motor-mount-base.stl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]
2023-05-08 motor mount T3
    [ab-motor-mount-new.FCStd]
2023-05-25 complete all main motion parts
    [140p0-jig.stl, 1x_extrudion-end-serial-template.stl, 1x_extrusion-end-logo.stl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]
2023-06-03 update frame drawing
    [5v-acdc-usb-box.FCStd, back-cable-mounter.FCStd, bear-fs-cover-e3d-collet.stl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]
2023-06-04 updat frame assembly/bom
    [frame-assembly.FCStd, frame-bracket.FCStd, lcd-mounter-mini.FCStd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]
2023-06-08 fix hotend offset
    [dragon-face-mod.FCStd, spool holder.FCStd]
2023-06-10 update missing links in BOM
2023-06-13 update bom, add toolhead assembly
2023-06-14 update BOM, assembly
    [ab-motor-assembly.FCStd, bearings-pulleys-dilers.FCStd, frame-assembly.FCStd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]
2023-06-17 add aseembly step
    [5v-acdc-usb-box.FCStd, ab-motor-assembly.FCStd, ab-motor-mount.FCStd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]
2023-06-22 export STLs
    [140p0-jig.stl, 1x-z-rod-bottom-mount-pref.stl, 1x-z-rod-top-mount-pref.stl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]
2023-07-02 update CAD, add missing STLs
    [1x_aux-duct.stl, 1x_back-panel-bottom-left.stl, 1x_back-panel-bottom-right.stl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]
2023-07-04 fix screw size in assembly
    [back-panel-tmp.FCStd, back-panel.FCStd]
2023-07-05 fix assembly nut size
2023-07-06 update aux duct
    [1x_aux-duct-r6.stl, 1x_aux-duct.stl, 1x_back-panel-top-left.stl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]
2023-07-21 adjust bearing slot tolerance
    [1x_bottom-bearing-cap.stl, 1x_carrier-body.stl, 1x_top-bearing-cap.stl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]
2023-08-03 add panel mounts
    [2x_y-cover-cap-mirror.stl, 2x_y-cover-cap.stl, 4x_y-cover-body.stl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]
2023-09-16 update panel mounts
    [4x_y-cover-body.stl, panel-clip-assembly.FCStd, panel-clip-housing.stl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]
2024-02-08 update drawings
    [bed-assembly.FCStd, mk3-bed-drawing.FCStd, mk3-center-frame-drawing.FCStd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]
2024-03-14 add new z rod mount
    [1x-z-rod-bottom-mount-right-pref.stl, 1x-z-rod-top-mount-right-pref.stl, 2x-z-rod-bottom-mount-left-loose.stl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]
2024-03-14 add z-rod mount aligner
    [119p5-jig.stl, 42p5-jig.stl, z-rod-holder.FCStd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]
2024-03-14 update assembly
    [1x-z-rod-bottom-mount-pref.stl, 1x-z-rod-bottom-mount-right-pref.stl, 1x-z-rod-top-mount-pref.stl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]
2024-03-22 update 1x-z-rod-bottom-mount-right-pref.stl based on Apex's suggestion
    [1x-z-rod-bottom-mount-right-pref.stl, z-rod-holder.FCStd]
2024-03-24 update z rod mounts, add pom nut install tool
    [1x-z-rod-bottom-mount-right-pref.stl, 1x-z-rod-top-mount-right-pref.stl, 2x-z-rod-bottom-mount-left-loose.stl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]
2024-03-24 update rod mount aligner tool
    [z-rod-mount-aligner.FCStd, z-rod-mount-aligner.stl]
2024-03-27 add bearing stack holder tool
    [bearing-stack-holder-tool.stl]
2024-04-15 fix stl name
    [1x_left-motor-mount-cap.stl, 1x_left-motor-mount-spacer.stl, 1x_right-motor-mount-cap.stl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]
2024-04-18 add from frame logo stl
    [small-logo.stl]
2024-04-24 add motor support
    [1x_motor-support-body-left.stl, 1x_motor-support-body-right.stl, 1x_motor-support-slider-left.stl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]
2024-07-07 update readme, fix dgragon face stl
    [1x_dragon-face.stl, hotend-back-support.FCStd]
2024-07-09 add sample klipper conf
    [display.cfg, gcode.cfg, macro.cfg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]
2025-02-01 added back panel cover
    [1x_cable-panel-back-cover-1.stl, 1x_cable-panel-back-cover-2.stl, 1x_cable-panel-bottom-cover.stl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]
2026-02-08 Added custom retraction before cut to customize for special filaments that expand too much when cool after leave the hot zone and avoid a clog
    [tradrack_filamentcut.cfg]
2026-04-22 ProosaXY mini - Initial documentation (Print settings, bed assembly, readme)
2026-04-23 Added config section, initial config and some macros
    [printer.cfg, purge_line.cfg, snakeoil_homing.cfg]
2026-04-23 Klipper config documentation and wiring
2026-04-24 added stl files for proosa minii
    [1x_back-panel-bottom-left.3mf, 1x_back-panel-bottom-right.3mf, 1x_back-panel-connector-mmu.3mf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]
2026-04-24 added step files for proosa mini
    [Proosa Mini - panels.step, back-panel-bottom-left.step, back-panel-bottom-right.step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]
2026-04-24 printing document of proosa mini updated
2026-04-24 Added tools for proosa mini
    [silicon-mod-jig.3mf, silicon-mod-jig.step, z-rod-mount-aligner-mini.3mf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]
2026-04-24 proosa mini, z-axis assembly
2026-04-24 proosa mini - rear 20T idler assembly
2026-04-24 proosa mini , frame extrusions
2026-04-28 Proosa mini, flash klipper guide
2026-04-28 Proosa mini, Mini-y-carriage for lasercut
    [MINI-y-carriage.stp]
2026-05-06 Added bom links for proosa mini
2026-05-08 Proosa mini cad file for assembly
2026-05-13 Snakeoil test tool to calibrate shrink ratio and test bearing/rods/other assembly, before printing all parts.
    [snakeoil_test_tool.step, snakeoil_test_tool.stl]
2026-05-24 Front belt tensioners initial release for 8mm and 10mm rods
    [2x_front-tensioner-bearing-holder.stl, 2x_front-tensioner-cap.stl, 2x_front-tensioner-rod-holder-10mm.stl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]
2026-05-24 Rear live idlers initial release
    [1x_rear-live-idler-bottom-left.stl, 1x_rear-live-idler-bottom-right.stl, 2x_rear-live-idler-spacer-replace-16T.stl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]
2026-05-25 Fix title on rear live idlers readme
